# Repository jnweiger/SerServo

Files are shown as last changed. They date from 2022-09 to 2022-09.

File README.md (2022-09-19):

# SerServo
A serial line text protocol for a servo, using an arduino nano

This is used to drive the pointer on a 20cm diameter prehistoric ampere-meter.
It also features a ws2812 led-strip (also controlled through the serial protocol), and some 3d printed parts to implement this particular usecase of SerServo. Yes, the ampere-meter is now remote controlled ( - aka it is a fake).

## Wiring

I am using a bunch of dupont jumper cables, each with a male and female connector.
e.g. 3 male ends fit nicely into the standard servo connector, and the three losse ends with their female sockets, can be easily paced on the different positions on the arduino board.
Therefore I populated (ca. half of) the pin holes with pinheaders. The servo is usually color coded brown, red, orange.
Brown connects to a GND pin, red to +5V, and orange to D9.

The WS2812 LED strip comes with a round plug for power and a 3pin male connector.
The round plug is great for an external 5V 3A power supply, which is optional, since when keeping an eye of power consumption, the USB connector is sufficient. But when pushing LED brightness to its limits, and frantically driving the servo back and forth, a total of 3A migt be needed to avoid spurious resets.

Connect GND and +5V of the strip to the arduino board (even if you plan to use an external power supply)
There are two pins marked with GND, sufficient or both servo and strip. But only one pin is marked with +5V. A second (unlabeled) +5V pin can be found on the 6-pin (2x3) programming connector.
The data pin of the WS2812 connects via a 330 Ohm resistor to arduino pin D6.

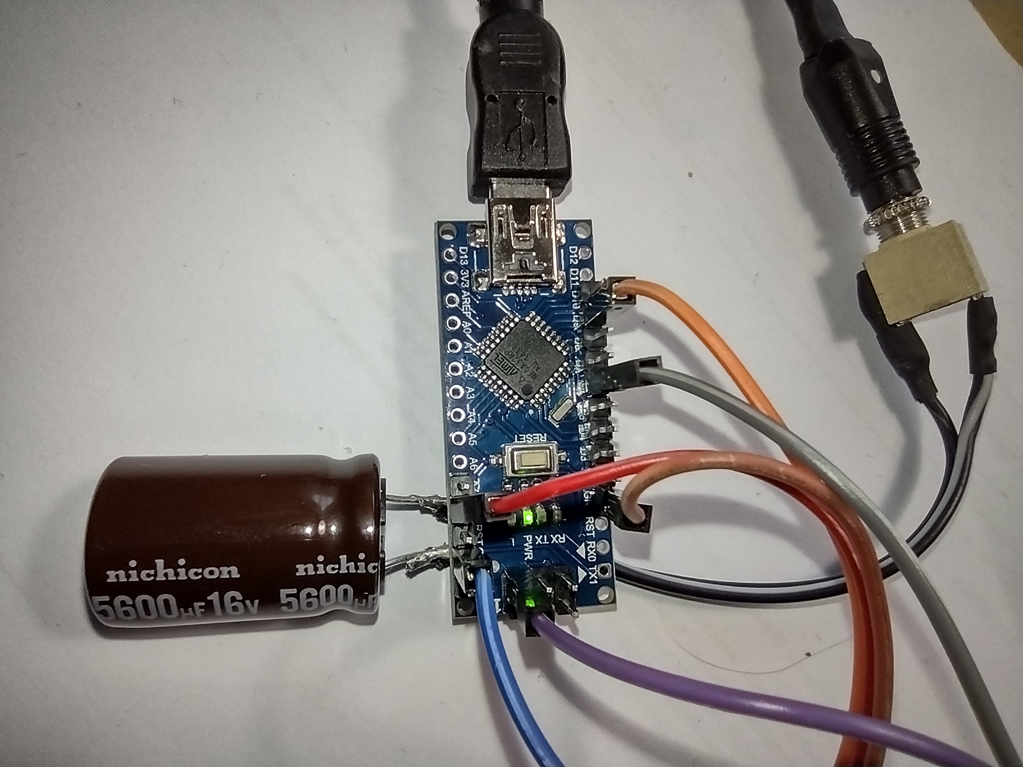
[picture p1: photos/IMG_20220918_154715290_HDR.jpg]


## Mechanics

In my case, a piece of 35 LEDs nicely fits around inside circumference. You can glue the strip with its adhesive side directly to the cover. It may or may not stick well enough. Especially during assembly, when the cables move, it might come off.
I designed a 3D-printed mounting ring for this. LEDs sit on the outside of the ring, facing inwards, so make sure to use some material that shines through nicely. I used white PETG, which seems good enough, although transparent should work better.
The adhesive side of the strip is then only used to wrap some other tape around the strip, so that it is held in place on the ring.

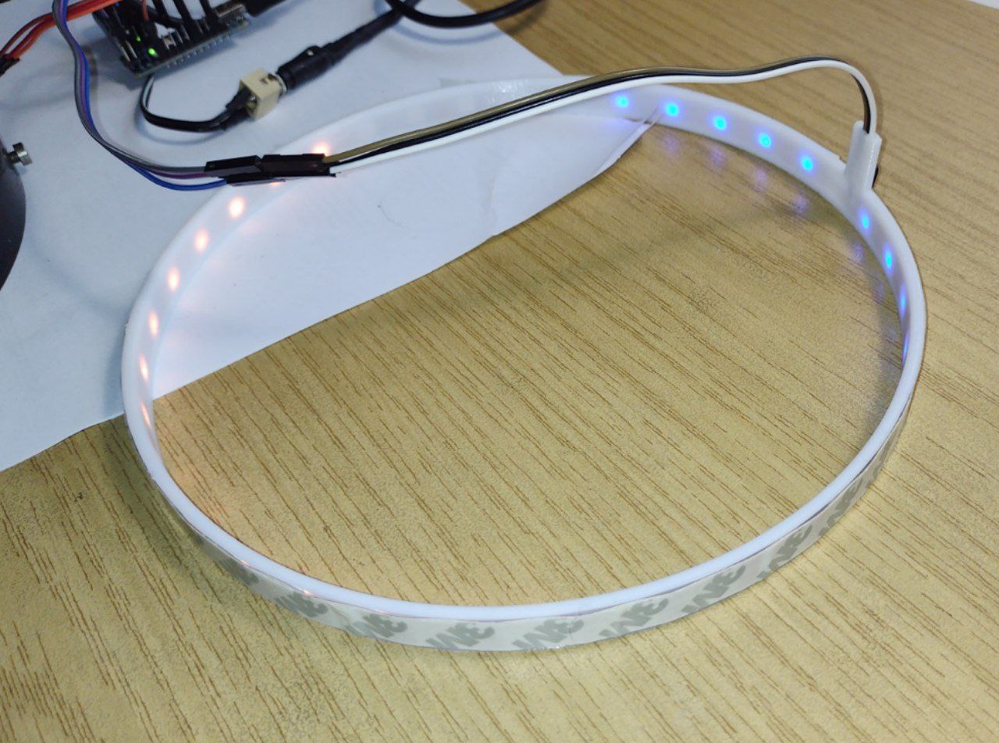
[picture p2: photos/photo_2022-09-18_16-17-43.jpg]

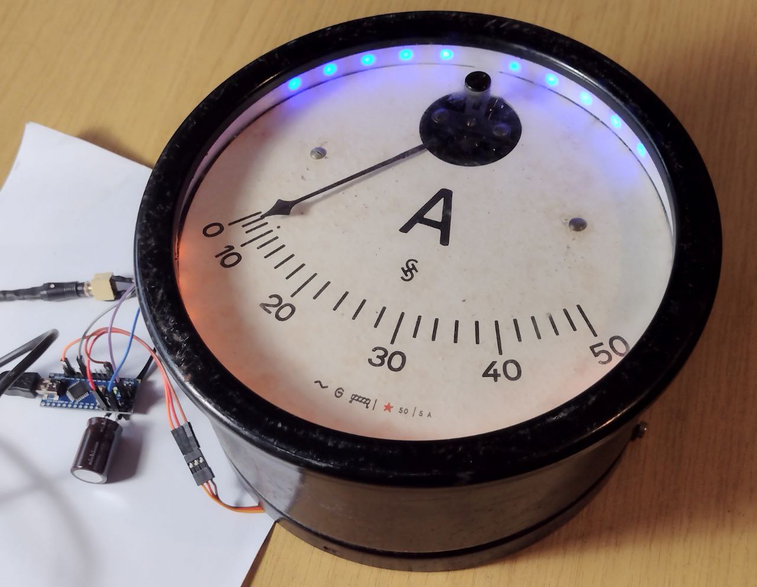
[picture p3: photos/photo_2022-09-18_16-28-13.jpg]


## USB-serial

The baud rate is 115200, no parity, two stop bits.

### Power supply
To simplify the circuit, we try to use the USB line also as a 5V power source.
According to https://www.arduino.cc/en/uploads/Main/ArduinoNano30Schematic.pdf, USB is coupled to the onboard +5V pins with a 0.5A Schottky diode MBR0520, so the total current draw should not exceed this value. The Schottky diode is actually there to allow us to connect both USB power and if needed an external
5V power supply without any problems.

The micro-servo can draw up to 1A, when under load or when moving at high speed.
The LED-strip can use max 60mA per LED, when all 3 channels R,G,B are at full brightness. This is a total of 2.1A + 1A ... -- which would not work via USB power.

#### Precautions
- The arduino nano schematics has a 100 nF and 4.7 uF capacitor on the USB side.
- We provide an external 5600 uF capacitor to buffer motor spikes.
- There is a default B brightness setting, that dims all values to below 50%.
- The default illumniation powers only the bottom half of the ring, at a dim orange.
- We use a custom servo driver that only sends a few pulses when moving, then stops the PWM, so that the motor gets powered down.
- We remember the previous PWM position and move the motor slowly towards the next set position to save power.

#### Power up and power down

The standard arduino setup() function is used to initialize the serial line, servo and led strip.
The servo is moved to position 0, the bottom half of the led strip starts glowing.

At power down, we "plan to" return the servo to position 0 before power really runs out.
To do so, we use the energy stored in the big 5600 uF capacitor together with a hardware modification on the arduino nano board:
- Connect pin D12 with the positive end of the 4.7uF onboard capacitor. This can be done with a short piece of wire soldered onto the pads, which are only 2mm apart.
- Bridge the capacitor with a 1k discharge resistor.

At powerloss, the schottky diode immediately disconnects USB power and the +5V rails. At pin D12 we detect the USB power loss (due to the discarge resistor), while the +5V rails still provide power. This allows us, to send one last motor moveto(0) command (at full speed!) and hope for the best.

This mimics what an original analog hardware meter would do. It might also help us to savw power at the next startup, as the servo is already at the desired position.

## Commands
Commmands start with a letter, can contain any amount of whitespace (ignored).
Then (optionally) decimal numbers follow, separated by whitespace, the command ends in a newline and or carriage retun
An empty command is ignored.

<pre>
P [x]
	x defaults to 0. Moves the servo to a position 0...1000
O
	Report servo calibration offsets.
O min max
	Set servo calibration offsets. For identity use: O 0 100.

B
	Report LED brightness setting.
B nn
	Set LED brightness in percent for subsequent C commands, default 50.
C
	Set all LEDs to 255, 255, 255
C x
	Sets all LEDs to color r=x, g=x, b=x	(0..255)
C r g b
	Sets the RGB value of all LEDs
C r g b n
	Set only LED n to the r g b value. n in 0..34)
	All other LEDs remain as they are.
C r g b n m
	Set LEDs n to m (inclusive)

H
?
	Print the above command summary.
</pre>

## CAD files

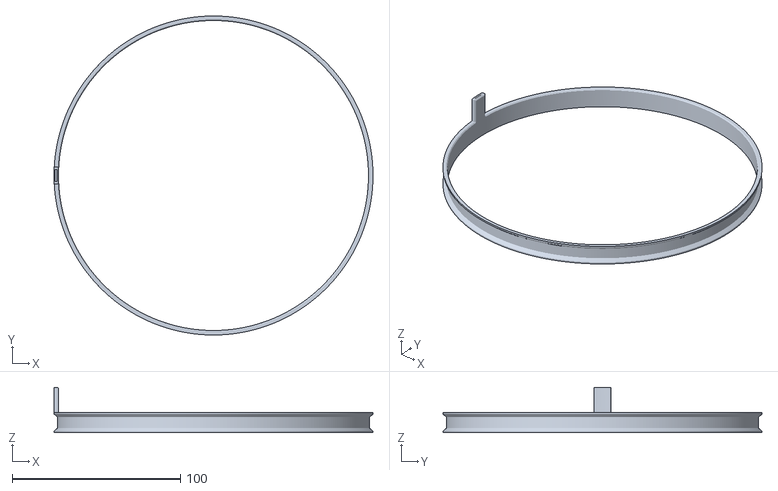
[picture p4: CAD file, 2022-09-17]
mechanics/LED-Ring-Body.stl
189.7 x 189.7 x 27.0

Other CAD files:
mechanics/LED-Ring.FCStd

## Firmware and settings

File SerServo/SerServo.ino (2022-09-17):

// SerServo 0.1
// (C) 2022 jw@owncloud.com, distribute under GPLv2 or ask
//
// Calibration of unit 1: min 33, max 102

// include the Servo library
#include <Servo.h>
// and make some light...
#include <Adafruit_NeoPixel.h>

Servo servo;

#define SERVO_PIN 9
#define SERVO_MIN_DEF 33	// p 0 moves to the 0 positon on the display
#define SERVO_MAX_DEF 102	// p 100 moves to the max value on the display
#define SERVO_UPDATE_INCR 0.005	// how much to increment or decrement the servo per update() call. (speedlimit)
#define SERVO_EPS	0.00001	// don't move, if within that tolerance.

#define WS2812_PIN 6
#define NUM_PIXELS 35  // how many LEDs we have

#define LED_DIM_ORANGE 40, 20, 0
#define LED_DIM_BLUE 0, 0, 40

#define LED_BOTTOM_DEFAULT_COLOR LED_DIM_ORANGE
#define LED_TOP_DEFAULT_COLOR LED_DIM_BLUE
#define LED_BOTTOM_HALF 8
#define LED_TOP_HALF 5

#define VERSION "0.5"

#define DUMMY 0

#if DUMMY
#include <string.h>

struct Serial
{
    int (*available)();
    int (*read)();
    void (*print)(char *);
} Serial;

struct servo
{
    void (*write)(int);
} servo;

#endif

Adafruit_NeoPixel pixels(NUM_PIXELS, WS2812_PIN, NEO_GRB + NEO_KHZ800);

void usage(char *s);
void set_led(int n, int r, int g, int b);
void moveto(int n);

struct cmd {
  unsigned char letter; // the letter seen, converted to upper case.
  int val[5];   // any decimal parameter seen
  int nval;   // number of valid numbers in values 0..5
  int more;   // 1: last seen some digit
} cmd = { '\0', { 0, 0, 0, 0, 0}, 0, 0 };

static unsigned char led_brightness[256];

struct cfg {
  int servo_min;
  int servo_max;
} cfg = { SERVO_MIN_DEF, SERVO_MAX_DEF };

struct state {
  double current;
  double moveto;
} state = { 40.0, .0 };		// we do a little movement when resetting.

void do_cmd()
{
  if (cmd.letter == '\0')
    return;

  if (cmd.letter == 'P')
    {
      if (cmd.nval == 0) cmd.val[0] = 0;  // position defaults to 0
      moveto(cmd.val[0]);
    }

  else if (cmd.letter == 'O')
    {
      if (cmd.nval == 2)
        {
	   cfg.servo_min = cmd.val[0];
	   cfg.servo_max = cmd.val[1];
        }
      else
        {
           Serial.print("servo_min=");
	   Serial.print(cfg.servo_min);
           Serial.print(" servo_max=");
	   Serial.print(cfg.servo_max);
           Serial.print("\n");
        }
    }

  else if (cmd.letter == 'B')
    {
       if (cmd.nval == 0)
         {
           Serial.print(int(0.5+(100*led_brightness[255] >> 8)));
	   Serial.print("\n");
         }
       else
	 {
	   double b;
	   b = 0.01 * cmd.val[0];
	   if (b > 1.0) b = 1.0;

	   for (int n = 0; n < 256; n++)
	     {
	       int v = int(n * b + .5);
	       Serial.print(v);
	       Serial.print("\n");
	       led_brightness[n] = v;
	     }
	}
    }

  else if (cmd.letter == 'C')
    {
      if (cmd.nval == 0) cmd.val[cmd.nval++] = 255;   // default full bright white
      if (cmd.nval == 1) cmd.val[cmd.nval++] = cmd.val[0];  // copy r to g
      if (cmd.nval == 2) cmd.val[cmd.nval++] = cmd.val[1];  // copy g to b
      int n = 0; int m = NUM_PIXELS;
      if (cmd.nval >= 4) n = m = cmd.val[3];
      if (cmd.nval == 5)     m = cmd.val[4];
      if (n < 0 || n > NUM_PIXELS) { usage("bad LED idx"); return; }
      if (m < 0 || m > NUM_PIXELS) { usage("bad second LED idx"); return; }
      while (n <= m)
        {
          set_led(n, cmd.val[0], cmd.val[1], cmd.val[2]);
          n++;
        }
    }

  else if (cmd.letter == 'H' || cmd.letter == '?')
    {
       Serial.print("\n\
\n\
P [x]\n\
  x defaults to 0. Moves the servo to a position 0...100\n\
\n\
O\n\
  Report servo calibration.\n\
\n\
O min max\n\
  Set servo calibration. For identity use 0 100.\n\
B nn\n\
  Set LED brightness in percent for subsequent C commands, default 50.\n\
C\n\
  Set all LEDs to 255, 255, 255\n\
C x\n\
  Sets all LEDs to color r=x, g=x, b=x  (0..255)\n\
C r g b\n\
  Sets the RGB value of all LEDs\n\
C r g b n\n\
  Set only LED n to the r g b value. n in 0..30)\n\
  All other LEDs remain as they are.\n\
C r g b n m\n\
  Set LEDs n to m (inclusive) \n\
\n");
    }

  else
    {
      usage("unknown command, try ?");
    }
  cmd.letter = '\0';
}

void usage(char *msg)
{
  Serial.print(msg);
}

void set_led(int i, int r, int g, int b)
{
  pixels.setPixelColor(i, pixels.Color(led_brightness[r], led_brightness[g], led_brightness[b]));
  pixels.show();
}

void moveto(int p)
{
  double x = p * 0.01 * (cfg.servo_max - cfg.servo_min) + cfg.servo_min;
  state.moveto = x;
}

void servo_update()
{
  double d = state.moveto - state.current;

  if (d > SERVO_EPS)
    {
      if (d > SERVO_UPDATE_INCR) d = SERVO_UPDATE_INCR;
      state.current += d;
      servo.write(state.current);
    }
  else if (d < -SERVO_EPS)
    {
      if (d < -SERVO_UPDATE_INCR) d = -SERVO_UPDATE_INCR;
      state.current += d;
      servo.write(state.current);
    }
  // else: it is close enough. Switch off the PWM?
}

void setup()
{
    Serial.begin(115200);
    Serial.print("SerServo v");
    Serial.print(VERSION);
    Serial.print("\n");

    servo.attach(SERVO_PIN);
    moveto(0);

    pixels.begin();
    pixels.clear();

    int n;
    for (n = 0; n < 256; n++)
       led_brightness[n] = int(n * 0.5 + .5);

    // The led ring starts and end at the top of the meter.
    // to illuminate the lower part, we find the center, and pad LED_BOTTOM_HALF to both sides.

#ifdef LED_BOTTOM_HALF
    for (n = ((NUM_PIXELS>>1)-LED_BOTTOM_HALF+1); n < ((NUM_PIXELS>>1)+LED_BOTTOM_HALF); n++)
       set_led(n, LED_BOTTOM_DEFAULT_COLOR);
#endif
#ifdef LED_TOP_HALF
    for (n = 0; n < LED_TOP_HALF; n++)
       set_led(n, LED_TOP_DEFAULT_COLOR);
    for (n = NUM_PIXELS - LED_TOP_HALF; n < NUM_PIXELS; n++)
       set_led(n, LED_TOP_DEFAULT_COLOR);  // dim orange
#endif
    Serial.print("default brightness 50%, default color 30 20 10\n");
    Serial.print("servo calibration: min=");
    Serial.print(cfg.servo_min);
    Serial.print(" max=");
    Serial.print(cfg.servo_max);
    Serial.print("\n");
}

void loop()
{
  servo_update();
  while (Serial.available() > 0)
    {
      int c = Serial.read();

      if (cmd.letter == '\0')
        {
          if (c == ' ' || c == '\t' || c == '\n' || c == '\r' ) continue; // ignore whitespace
          if (c >= 'a' && c <= 'z') c -= 'a'-'A';       // convert to upper case
          if ((c != '?') && (c < 'A' || c > 'Z')) { usage("Letter expected"); continue; }
          memset((void *)&cmd, 0, sizeof(cmd));
          cmd.letter = c;
        }
      else
        {
          if (c == ' ' || c == '\t')
	    {
	      if (cmd.more)
		{
		  if (cmd.nval >= 5) { cmd.letter = '\0'; usage("Too many numbers"); continue; }
	          cmd.nval++;
	        }
              cmd.more = 0;
              continue;
	    }
          if (c == '\n' || c == '\r')
            {
              if (cmd.more) cmd.nval++;
              do_cmd();
              continue;
            }
          if (c < '0' || c > '9') { cmd.letter = '\0'; usage("Digit expected"); continue; }
          cmd.val[cmd.nval] = 10 * cmd.val[cmd.nval] + c - '0';
          cmd.more = 1;
        }
    }
}


#if DUMMY
// dummy framework below
#include <sys/select.h>
#include <unistd.h>
#include <stdio.h>

int serial_available()
{
  fd_set rfd;
  struct timeval tv;

  FD_ZERO(&rfd);
  FD_SET(0, &rfd);
  tv.tv_sec = 0;
  tv.tv_usec= 10000;  // wait max 10 msec

  return select(1, &rfd, NULL, NULL, &tv);
}

void serial_print(char *msg)
{
  printf("serial_print(%s)\n", msg);
}

int serial_read()
{
  char buf[4];
  int c = read(0, (void *)&buf, 1);
  if (c != 1) return 0;
  return buf[0];
}

void servo_moveto(int p)
{
  printf("servo_moveto(%d)\n", p);
}

void usage(char *s)
{
  printf("usage(%s)\n", s);
}

void set_led(int n, int r, int g, int b)
{
  printf("set_led(n=%d, rgb = %d %d %d)\n", n, r, g, b);
}

int main()
{
  Serial.available = &serial_available;
  Serial.read = &serial_read;
  Serial.print = &serial_print;
  servo.moveto = &servo_moveto;

  for (;;) loop();
  for (;;)
  {
    if (Serial.available())
    {
      char c = Serial.read();
      printf("Seen %d = %c\n", c, c);
    }
  }
}
#endif

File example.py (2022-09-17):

#! /usr/bin/python3
#
# Exercise the SerServo API
# (C) 2022, jw@owncloud.com, distribute under GPLv2 or ask
#
# The pointer moves in steps from left to right, and back.
# While it moves left, three LEDS are green on the left side, while it moves to the right, they are on the right side.

import serial, sys, time

if len(sys.argv) < 2:
  print("\nUsage: %s PORT\n\nAvailable ports are:" % sys.argv[0])

  import serial.tools.list_ports as L

  for p in map(lambda x: x.device, L.comports()):
     print("  " + p)
  print("\n")
  sys.exit(1)

ser = serial.Serial(sys.argv[1], baudrate=115200, bytesize=serial.EIGHTBITS, parity=serial.PARITY_NONE, stopbits=serial.STOPBITS_TWO)

def slurp(ser):
  # slurp whatever is incoming.
  while ser.in_waiting > 0:
    print(ser.read(1))

def moveto(x):
  time.sleep(0.1)
  slurp(ser)
  ser.write(b"P %d\n" % x)
  time.sleep(0.1)

def led(r, g, b, first=None, last=None):
  if last is None: last = first
  time.sleep(0.1)
  if first is None:
    ser.write(b"C %d %d %d\n" % (r,g,b))
  else:
    ser.write(b"C %d %d %d %d %d\n" % (r,g,b,first,last))
  time.sleep(0.1)


while True:

  led(0,0,0,   6,  8)
  led(0,20,0, 26, 28)
  for i in (10, 20, 30, 40, 50, 60, 70, 80, 90, 100):
    moveto(i)
    time.sleep(1.5)

  led(0,20,0,  6,  8)
  led(0,0,0,  26, 28)
  for i in (80, 60, 40, 20, 0):
    moveto(i)
    time.sleep(1.5)

ser.close()

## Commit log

2022-09-16 added a few peliminary prototype photos
2022-09-17 thinner led ring.
    [LED-Ring-Body.stl, LED-Ring.FCStd]
2022-09-17 runtime calibration added
2022-09-17 clicketyclack with LED blinking..
2022-09-17 closed end of ring chimney
    [LED-Ring-Body.stl, LED-Ring.FCStd]
2022-09-17 speed limit implemented, brightness fixed.
    [SerServo.ino]
